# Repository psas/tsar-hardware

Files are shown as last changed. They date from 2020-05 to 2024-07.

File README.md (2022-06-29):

# Tsar Hardware
Hardware for the Test Stand Automation and Regulation project that runs [PSAS' Liquid Fuel Engine Test Stand](https://github.com/psas/liquid-engine-test-stand)

The TSAR system controls the test stand at a safe distance with several safety features in place. The system monitors the pressure, temperature, and valve states of the system. For automation software and controls see the [tsar software repo](https://github.com/psas/tsar-software). 

The OSGC Final UTEAP Report contains more detailed information and can be found [here](https://docs.google.com/document/d/1x4pjh9ZbApyyvRd1HysukK7K5CVWpYE1/edit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).

## Tsar Hardware System Architecture Block Diagrams

Below you can see the levels of block diagrams for the whole system,

### V -1

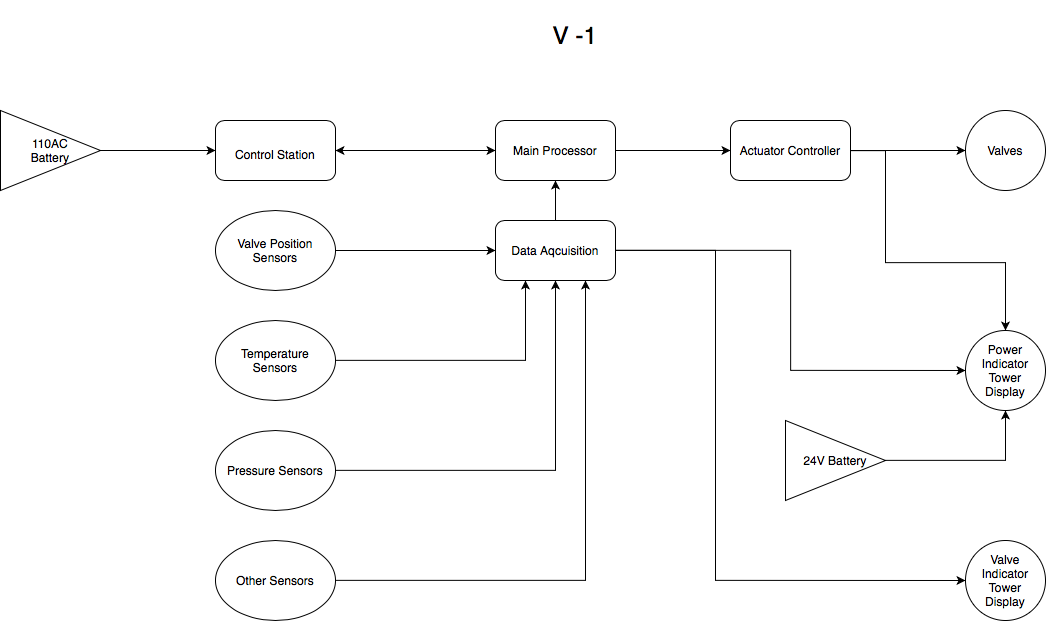
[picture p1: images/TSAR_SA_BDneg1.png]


### V 0

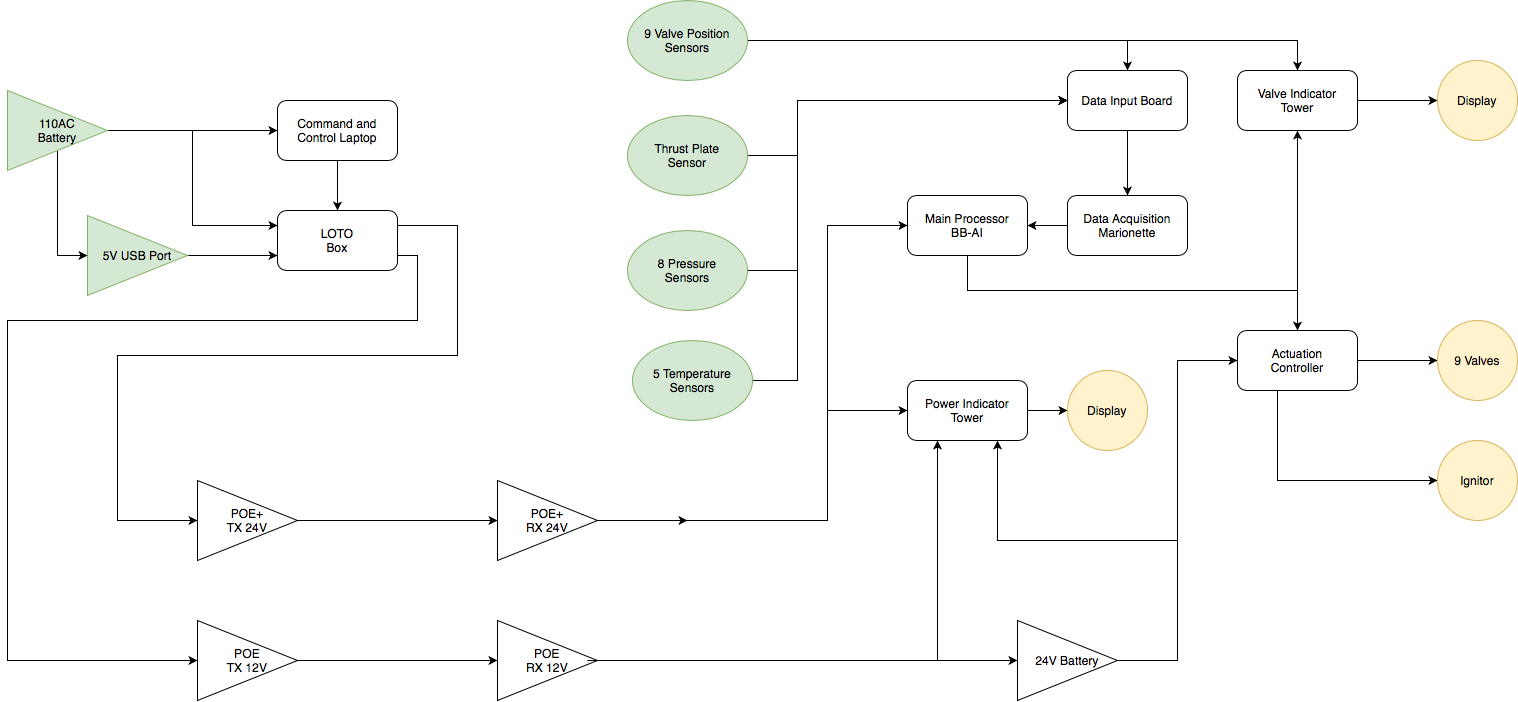
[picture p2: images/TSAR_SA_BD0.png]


### V 1

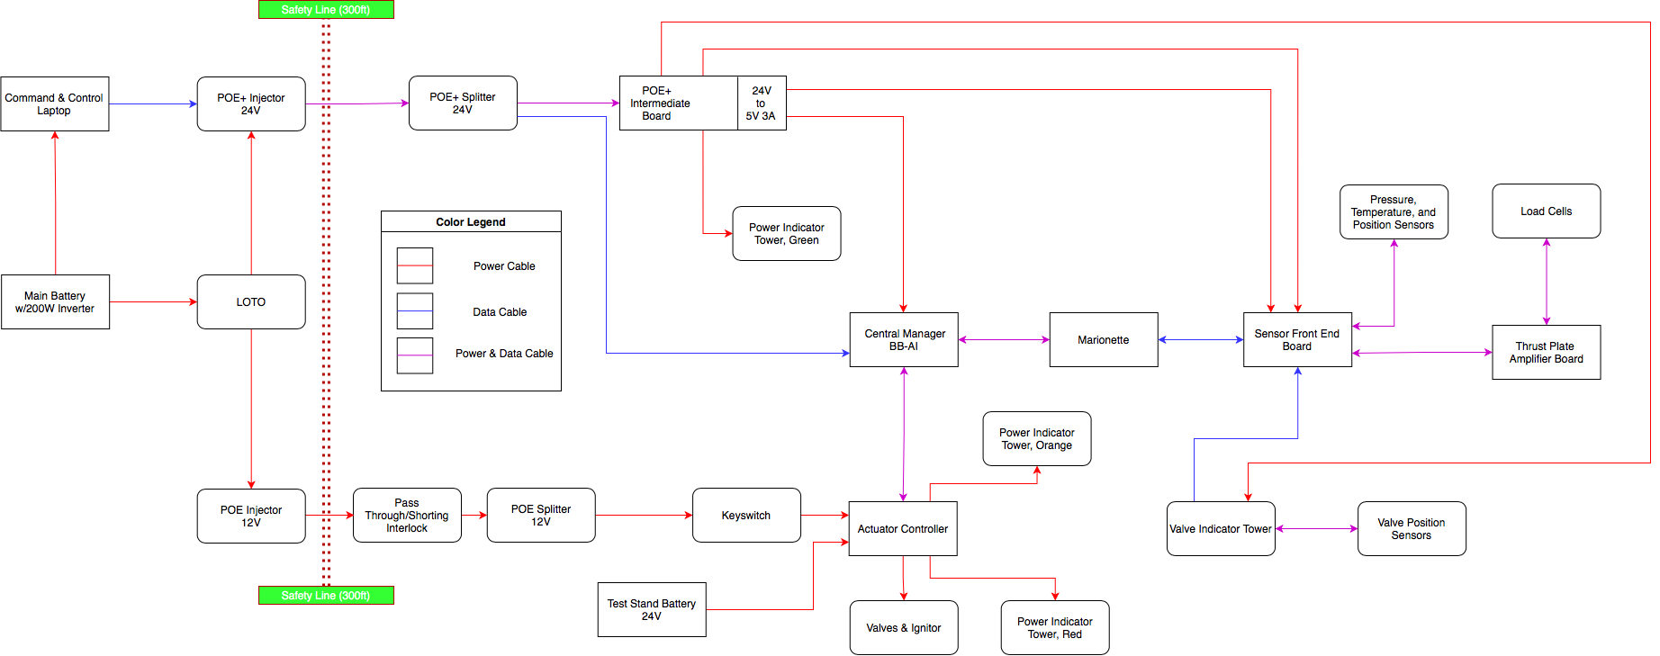
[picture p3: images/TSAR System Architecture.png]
sys_arch


## Systems Within the Repo

Within this repo there are several subsystems.

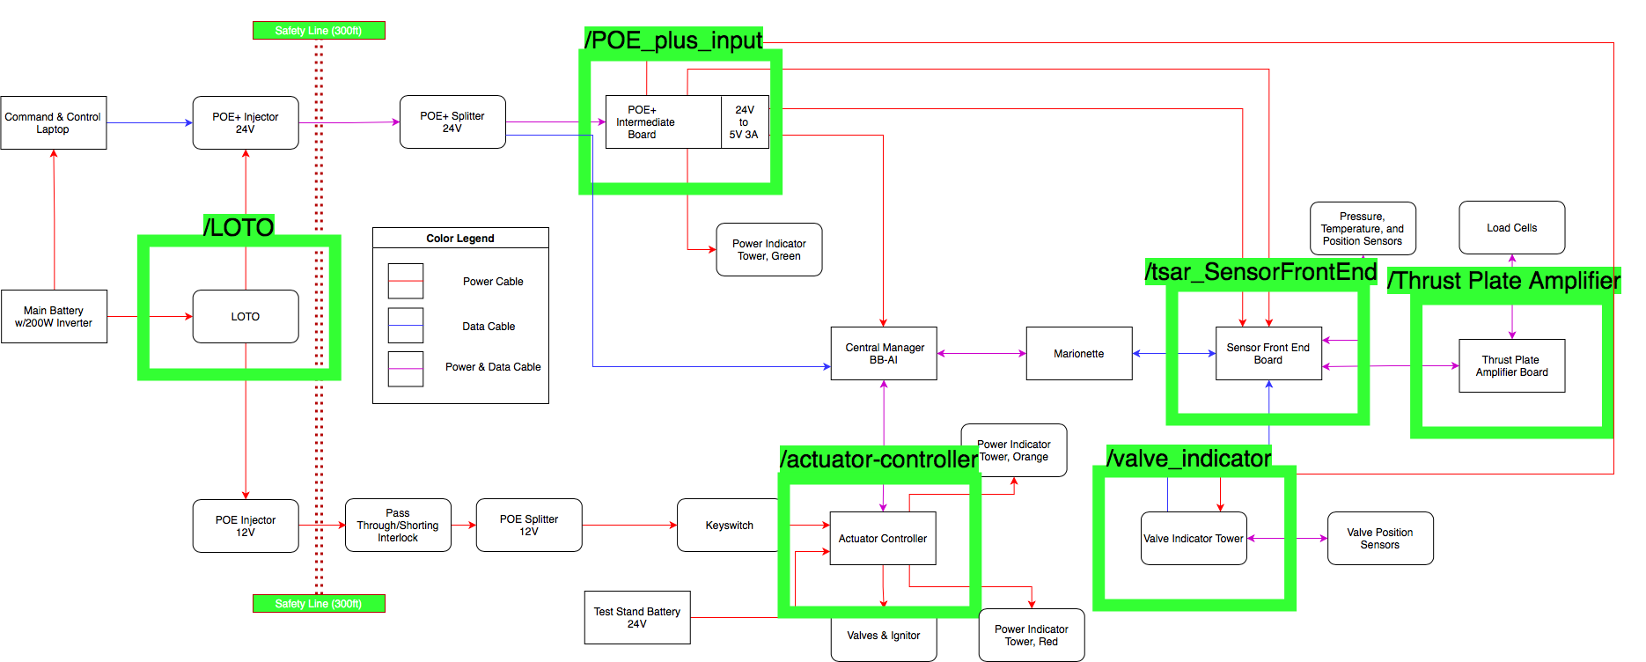
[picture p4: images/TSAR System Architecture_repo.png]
sys_arch


### [LOTO](https://github.com/psas/tsar-hardware/tree/master/LOTO)

The LOTO Repo is the Lock-Out Tag-Out subsystem.

This system prevents the test stand from being powered while key-holders are past the safety line. 

### [Thrust Plate Amplifier](https://github.com/psas/tsar-hardware/tree/master/Thrust%20Plate%20Amplifier)

The Thrust Plate Amplifier amplifies the thrust plate signal.

### [Actuator Controller](https://github.com/psas/tsar-hardware/tree/master/actuator-controller)

This board communicates with the BB-AI over UART and controls the valves. The processor is a STM32F0 using a Nucleo-board. 

For more information on the software for this board please see [Actuator Controller Code, Firmware](https://github.com/psas/tsar-software/tree/master/Actuator%20Controller%20Firmware) and [Actuator Controller Code, Test](https://github.com/psas/tsar-software/tree/master/Actuator%20Controller%20Test)

### [Tsar Sensor Front End](https://github.com/psas/tsar-hardware/tree/master/tsar_SensorFrontEnd)

This board collects the data from all of the sensors (temperature, pressure, thrust plate) and conditions the signals to send to the Marionette. 

### [Valve Indicator](https://github.com/psas/tsar-hardware/tree/master/valve_indicator)

This board collects the valve position data and compares it to the expected valve state. If there is an error it will display a code over LEDs to indicate which valve is misbehaving. 

For more information on the software for this board please see [Valve Indicator Code](https://github.com/psas/tsar-software/tree/master/valve_indicator)

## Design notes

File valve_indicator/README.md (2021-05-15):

# Eagle Schematics & Boards

## Valve Indicator

Purpose:
This board will collect valve position data using hall effect sensors mounted on nine solenoid valves and will report the current commanded state of the valves. 
The processor will compare the expected valve states with the correct reported valve states, 
if the states do not match the processor will output an indication over the LED arrays.
The LED arrays will display specific binary codes to indicate which valve does not match. 
If multiple valves do not match then the LED arrays will display all binary codes one after another based upon priority information.

Inputs:
- POE+ 24V Power
- UART Data
- Nine Hall Effect Sensors
- ST-Link V2 Emulator

Processor:
- STM32F042K

Outputs:
- Three LED Arrays
- One Buzzer
- SD Card Data Backup

### Libraries In Use

- Power Regulators: Diodes Inc. - AZ34063UMTR-G1.lbr
- Test Points: oresat-misc.lbr
- Processor: U-ST-STM32F042K-uC.lbr
- JTAG Emulator Connector: J-Samtec-FTSH-105-XXX-DV-K-ARM-SWD.lbr
- Diode: On Semiconductor - 1N5819G.lbr

### Design Rules

We are using the OshPark design rules for a 2-layer board.

### Safety Bar Level 0 Block Diagram:
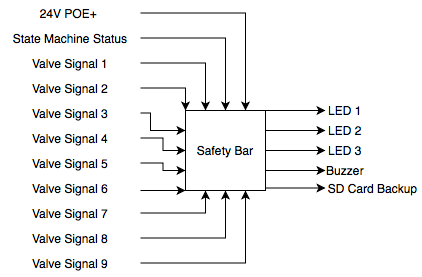
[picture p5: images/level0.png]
Level 0 Block Diagram


### Safety Bar Level 1 Block Diagram:
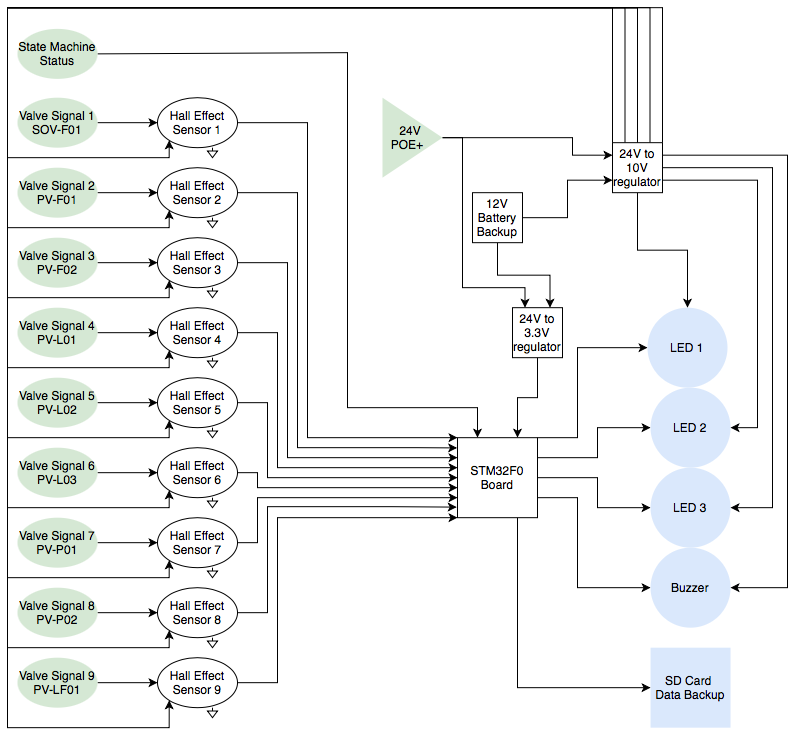
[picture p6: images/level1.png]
Level 2 Block Diagram


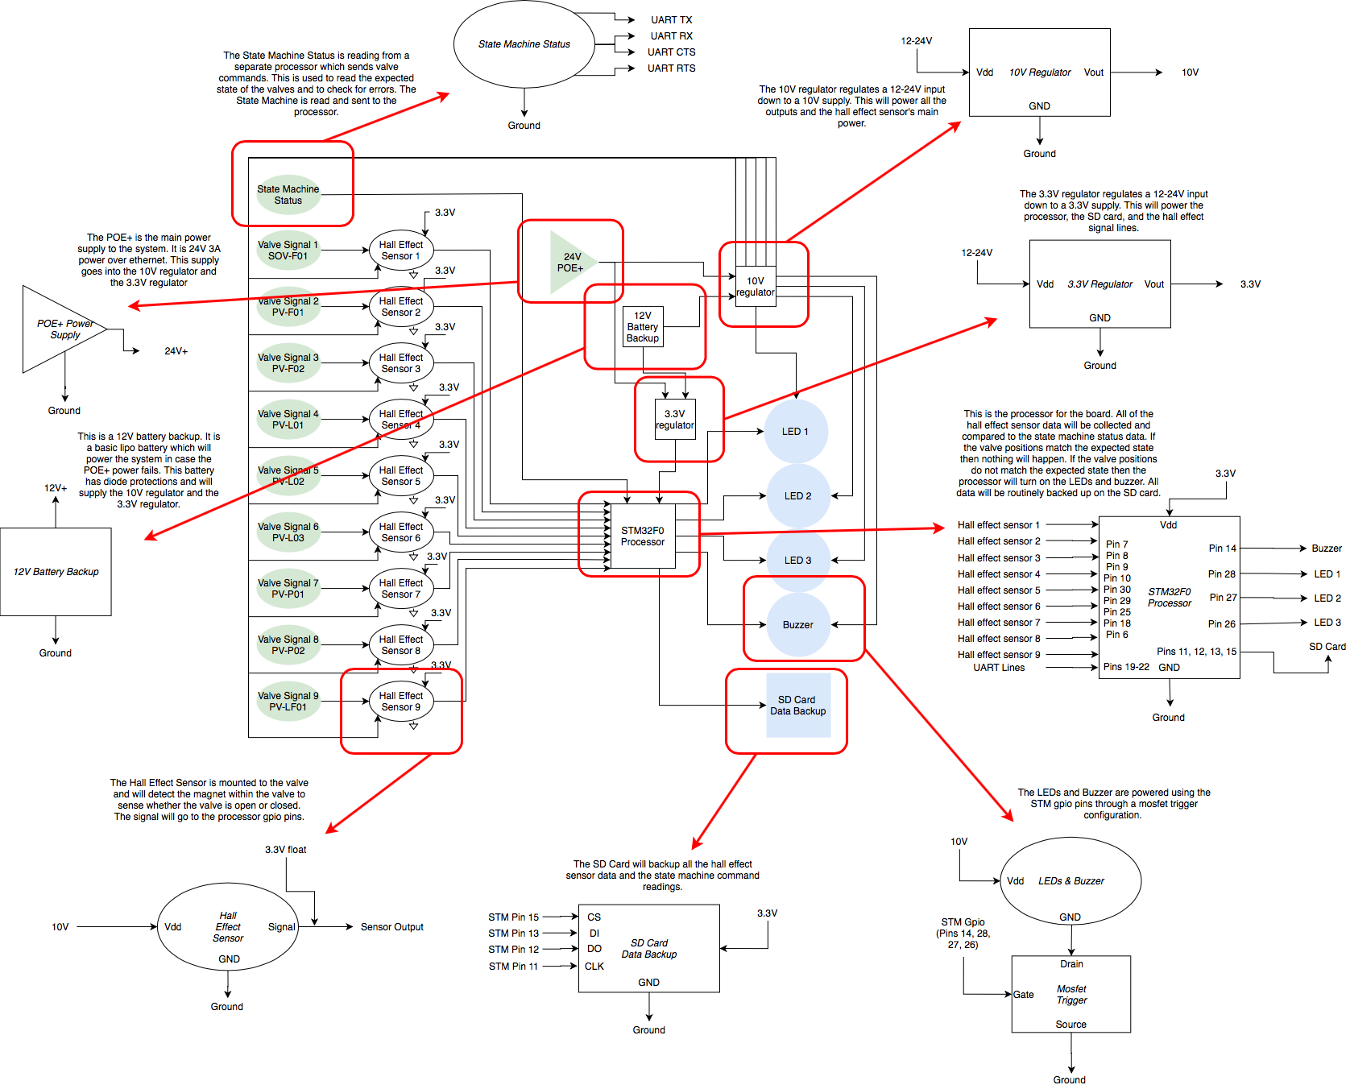
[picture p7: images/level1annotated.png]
Level 2 Block Diagram


### Extra Pinout
This board is equipped with a 32 pin header to access all unused STM32 pins.

1. PB2
2. +10V
3. PB10
4. PC9
5. PB11
6. PC8
7. PB12
8. PC1
9. PB13
10. PC10
11. PB14
12. PC4
13. PB15
14. PC5
15. PC11
16. PC6
17. GND
18. PC7
19. GND
20. PC12
21. PD2
22. PC3
23. PC14-OSC32_IN
24. BOOT0
25. PC13
26. PB9
27. +3V3
28. PC0
29. PC15_OSC32_OUT
30. PC2
31. GND
32. GND

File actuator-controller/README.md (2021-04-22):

# Actuator Controller

All valve and ignitor control is done via the Actuator Controller, which is currently implemented using a Nucleo mounted on a PCB. 

This board reads commands and data from the BeagleBone-AI over USB cable which it uses to switch test stand states and perform an Automatic Shutdown in the event of a system failure. Failure is defined as non-nominal sensor conditions; meaning that if pressure and/or temperature readings are outside of nominal ranges or if the physical state of the valves do not match the expected state of the valves (i.e. a valve is potentially stuck or frozen) then the system will go into an automatic shutdown state. The automatic shutdown state purges all propellants from the lines, depressurizes the system, and returns all valves to the Safety State (unpowered). This Automatic Shutdown can be triggered by the Actuator Controller automatically and it can be commanded by the user. 

The Actuator Controller requires a consistent heartbeat and emergency response code. If for some reason this heartbeat stops, or any other emergency indicator is tripped, the Actuator Controller will execute the emergency shutdown routine in accordance with the emergency response code most recently sent.

The Actuator Controller is also connected via UART to the Valve Indicator board. This connection is solely for sending the current state updates to the Valve Indicator board for other purposes. There is no data coming to the Actuator Controller from the Valve Indicator. 

The Nucleo board is powered by the USB cable from the BeagleBone-AI. The valves and ignitor are powered by a 24V power input coming from the Test Stand Battery. There is one 24V to 12V regulator on this board, it is used for an valve which runs at 12V; all other valves run at 24V. The 24V battery power is isolated from the Nucleo by the Mosfet circuits on sheet 2; the GPIO pins from the Nucleo trigger the Mosfets and allow the 24V power to switch on or restrict off the valves.

## Actuator Controller Block Diagram

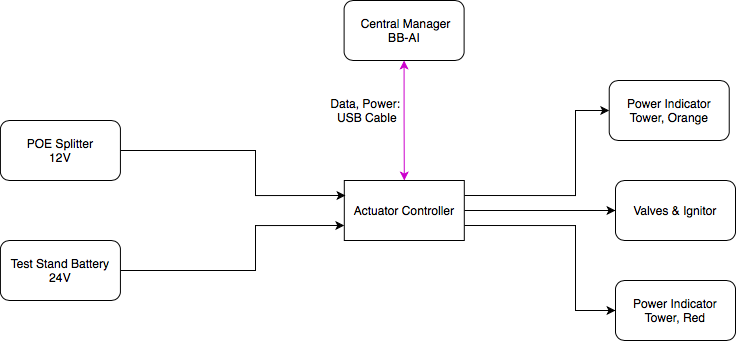
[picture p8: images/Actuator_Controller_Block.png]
ac_block


## Actuator Controller Software

All actuator control software and documentation can be found [here](https://github.com/psas/tsar-software). Specifically, [the testing software](https://github.com/psas/tsar-software/tree/master/Actuator%20Controller%20Test), [the firmware](https://github.com/psas/tsar-software/tree/master/Actuator%20Controller%20Firmware), and [the state machine](https://github.com/psas/tsar-software/tree/master/state-machine)

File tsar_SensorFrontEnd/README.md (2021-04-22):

The Sensor Front End board is an intermediate board which connects various test stand sensors to the data acquisition system. This board is intended to interface sensors with the Marionette DAQ Rev2.2. The Marionette documentation and board files can be found at https://marionette-daq.github.io/ 

The board allows connections for 44 analog sensors. These are broken into 14 channels which go through this board and to the Marionette board and 30 on this board, which connect to the Marionette via SPI.  Signals sent to the Marionette should be limited to the  0-3V range.

Currently (4/16/21), the 14 channels which go through this board and to the Marionette's ADC are  on sheet 2: Analog and consist of the 4 load cell sensors for thrust detection and 10 4-20mA pressure sensors which are labeled for either 1k PSI or 3k PSI. The signals go through TVS circuit protection before they are sent to the Marionette. The load cells are speced to TE Connectivity MPN: FC2311-0000-1000-L while the pressure sensors are speced to TE Connectivity 1k Sensors: 824-M305100000501KPG and 3k Sensors: M3051-000005-05KPG.

Currently (4/16/21), the 30 channels which are on this board go through TVS circuit protection, to an ADC chip (ADS7953QDBTRQ1), and then sent over SPI to the Marionette; these sensors can be found on sheet 3: Digital and sheet 4: Extra Sensors. These 30 channels consist of 7 thermocouples for temperature sensing, 9 hall effect sensors for valve position sensing, and 14 extra sensor lines which are unallocated. Note: The hall effect sensor lines come from the Valve Indicator board rather than directly from the sensors. 

The ADC channels on the Marionette sample 12-bits at up to 1Msps. The Front End board ADC channels sample 16-bits at 100ksps, which is sent to the Marionette over SPI.

There are 2 power regulators and two power inputs on this board. This board receives 24V from the POE Input Board and 5V from the POE Input Board. The two regulators take the 24V power and step it down to both 12V and 3V3. The 24V input serves as the main power source. The 12V power is used for the Pressure Sensors and is sent off board to the Thrust Plate Amplifier Board. The 5V power is used for the thermocouple amplifier circuits and the ADC reference voltage signal. The 3V3 line is used for the ADC chips. 

## Sensor Front End Block Diagram

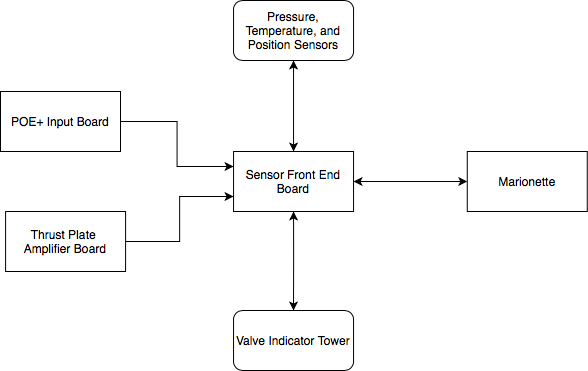
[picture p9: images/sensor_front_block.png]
Level 1 Block Diagram


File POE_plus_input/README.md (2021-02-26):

# POE Plus Input Board

This board takes the main low risk POE+ 24V input and splits it off to provide 24V power to the Valve Indicator Board and the Sensor Front End board. It has a 24V to 5V regulator which provides power to the Central Manager (BB-AI) and the Sensor Front End board. 

## POE+ Block Diagram

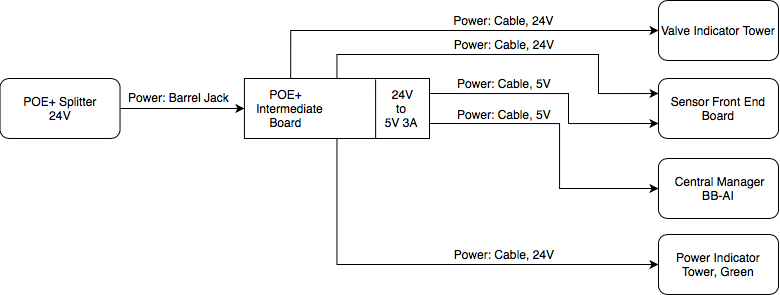
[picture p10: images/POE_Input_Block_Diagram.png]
Level 1 Block Diagram


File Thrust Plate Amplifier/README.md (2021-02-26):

# Thrust Plate Amplifier

This board amplifies the signals of the four load cells present on the thrust plate. The thrust plate measures the thrust of the liquid fuel engine. The load cells are compression only using part number FC2311-0000-1000-L. The signals from the amplifier are sent to the Sensor Front End board. This amplifier board must be as close as possible to the load cells on the thrust plate; otherwise the signals will be degraded and invalid. 

The thrust plate amplifier is powered by the Sensor Front End board's 12V rail.

## POE+ Block Diagram

Level 1 Block Diagram

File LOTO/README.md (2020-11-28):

# LOTO Key Indicator

There are nine of these boards mounted in the LOTO box. Each board indicates the safety keys status and powers the system if all safety keys are in place. There are LED indication lights, green indicates that the key is in place, red indicates that the key is not in place. 

## Level 0 Block Diagram

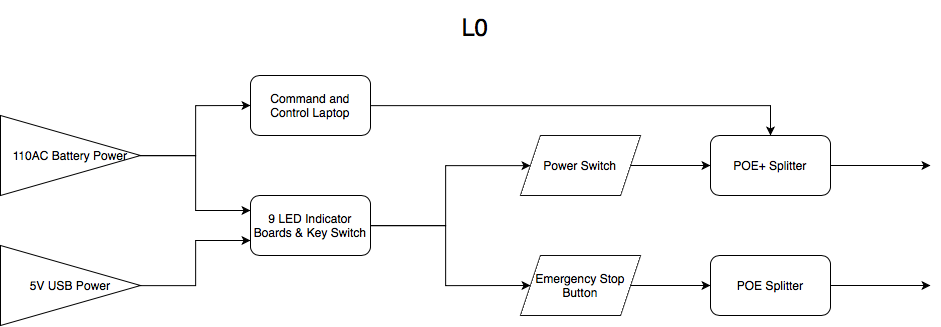
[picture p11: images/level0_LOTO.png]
l0loto


## Level 1 Block Diagram

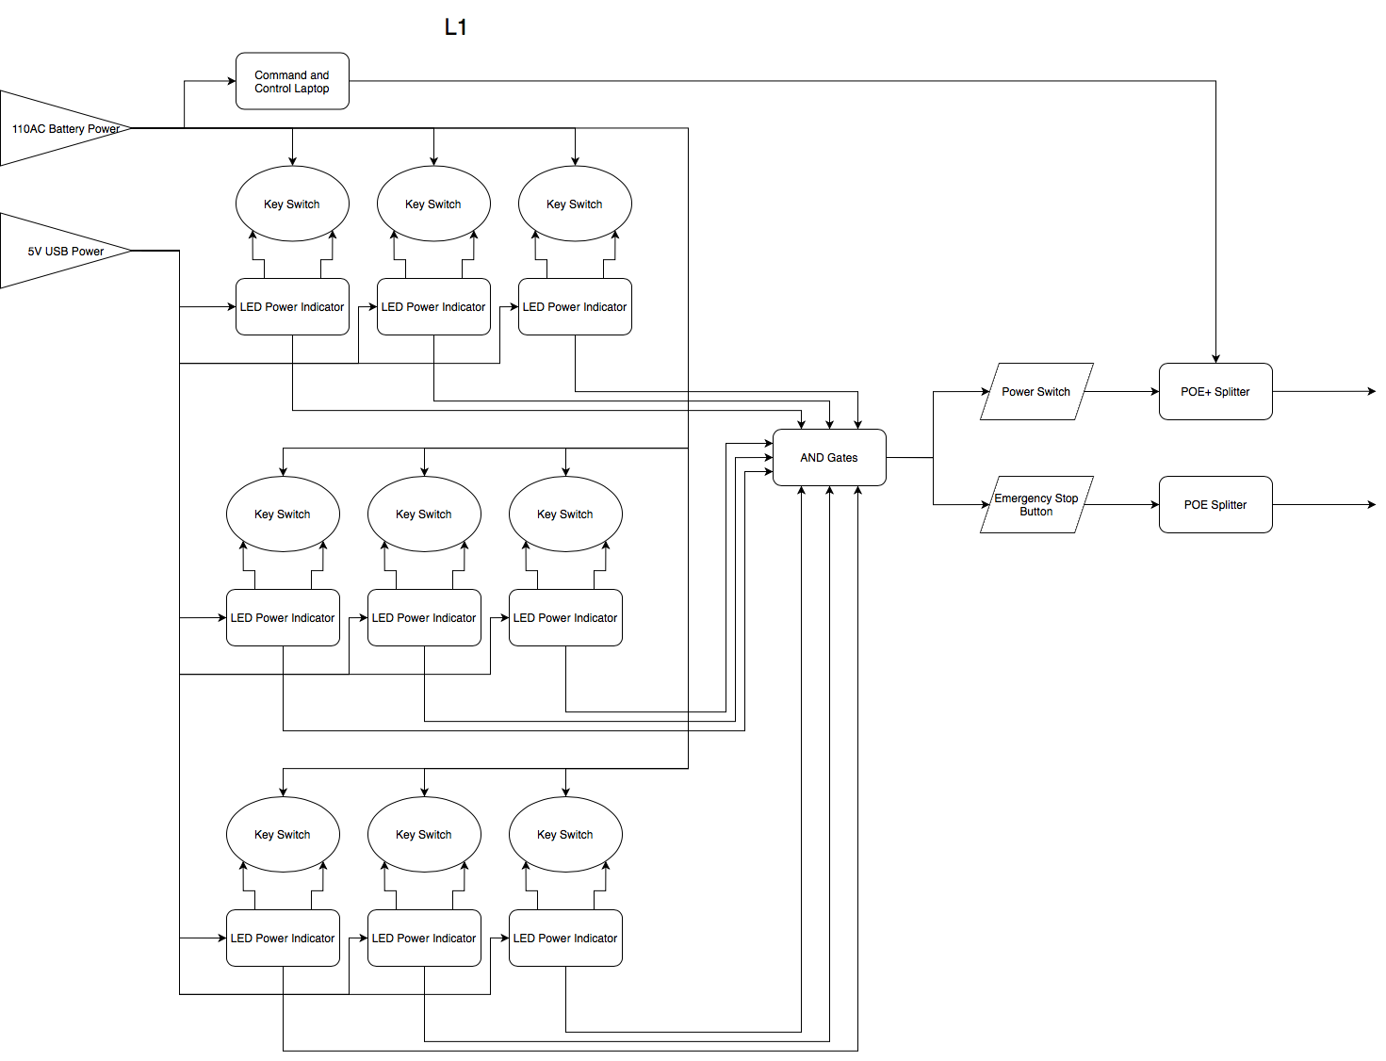
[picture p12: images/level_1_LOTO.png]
l1loto


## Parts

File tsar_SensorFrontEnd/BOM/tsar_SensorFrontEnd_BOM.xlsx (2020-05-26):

Status | Qty | Reference Designator | Description | Value | Manufacturer Part Number | Price (Individual) | Price X Quantity | Manufacturer | Product Link | Package
 | 26 | C1-C10, C16-C18, C20, C21, C28-C30, C35-C42 |  | 120 pF | C0805C121KDRACTU | $0.54 | $14.04 | Würth Elektronik | https://www.digikey.com/product-detail/en/kemet/C0805C121KDRACTU/399-7139-1-ND/3439332 | C0805
 | 6 | C12, C15, C23, C24, C27, C31 | 0.1uF Cap for 3V3/5V PSU | 0.1uF | GCM21BR72A104KA37L | $0.22 | $1.31 | Murata Electronics | DigiKey (https://www.digikey.com/product-detail/en/murata-electronics/GCM21BR72A104KA37L/490-4789-1-ND/1641708) | C0805
 | 6 | C11, C13, C14, C32-C34 |  | 1 uF | CL21A105KACLNNC | $0.15 | $0.90 | Samsung Electro-Mechanics | https://www.digikey.com/product-detail/en/samsung-electro-mechanics/CL21A105KACLNNC/1276-2395-1-ND/3890481 | C0805
 | 2 | C19, C25 | 10uF Cap for 3V3/5V PSU | 10uF | C0805C106K8PACTU | $0.12 | $0.23 | Murata Electronics | https://www.digikey.com/product-detail/en/murata-electronics/GRM21BR61E106KA73L/490-5523-1-ND/2334919 | C0805
 | 2 | C22, C26 |  | 4.7 uF | CL21A475KAQNNNE | $0.15 | $0.30 | Samsung Electro-Mechanics | https://www.digikey.com/product-detail/en/samsung-electro-mechanics/CL21A475KAQNNNE/1276-1244-1-ND/3889330 | C0805
 | 1 | POE_BYPASS | Bypass Cap from +12V POE | 100uF | ECA-1HM101 | $0.31 | $0.31 | Panasonic | https://www.digikey.com/product-detail/en/panasonic-electronic-components/ECA-1HM101/P5182-ND/245041 | Radial, Can
 | 26 | D1 - D26 | 5V TVS Diode | 5V TVS | D5V0H1U2LP1610-7 | $0.38 | $9.88 | Diodes Incorporated | https://www.digikey.com/product-detail/en/diodes-incorporated/D5V0H1U2LP1610-7/D5V0H1U2LP1610-7DICT-ND/8125969 | D0603
 | 2 | D27, D28 | Diode for Voltage Regulators | DFLS160 | DFLS160 | $0.44 | $0.88 | Diodes Incorporated | https://www.digikey.com/product-detail/en/diodes-incorporated/DFLS160-7/DFLS160DICT-ND/765636 | DO214AA
 | 27 | JP1 - JP27 | 1x 03 headers for unpopulated sensor channels |  |  |  |  |  |  | 3X 1 pin
 | 26 | R11-R20, R27-R29, R31, R32, R39, R40, R41, R47, R49, R54, R56, R58, R60- R62 | TVS Resistors for output | 1 K | RC0805FR-071KL | $0.10 | $2.60 | Yageo | https://www.digikey.com/product-detail/en/yageo/RC0805FR-071KL/311-1-00KCRCT-ND/730391 | R0805
 | 12 | R3-R10, R21-R24 | Pressure sensor Resistors, Cryo SensorResistors | 150 | RNCP0805FTD150R | $0.10 | $1.20 | Stackpole Electronics Inc | https://www.digikey.com/product-detail/en/stackpole-electronics-inc/RNCP0805FTD150R/RNCP0805FTD150RCT-ND/2240550 | R0805
 | 1 | R25 |  | 22k | RC0805FR-0722KL | $0.10 | $0.10 | Yageo | https://www.digikey.com/product-detail/en/yageo/RC0805FR-0722KL/311-22-0KCRCT-ND/730683 | R0805
 | 1 | R26 | Output-setting resistor for switching power supply | 124k | RK73H2ATTD1243F | $0.10 | $0.10 | KOA Speer Electronics, Inc. | https://www.digikey.com/product-detail/en/koa-speer-electronics-inc/RK73H2ATTD1243F/2019-RK73H2ATTD1243FCT-ND/10234967 | R0805
 | 2 | R30, R36 |  | 23.7k | RK73H2ATTD2372F | $0.10 | $0.20 | KOA Speer Electronics, Inc. | https://www.digikey.com/product-detail/en/koa-speer-electronics-inc/RK73H2ATTD2372F/2019-RK73H2ATTD2372FCT-ND/10235460 | R0805
 | 2 | R33, R37 |  | 10k | RN73R2ATTD1002F25 | $0.39 | $0.78 | KOA Speer Electronics, Inc. | https://www.digikey.com/product-detail/en/koa-speer-electronics-inc/RN73R2ATTD1002F25/2019-RN73R2ATTD1002F25CT-ND/11476953 | R0805
 | 1 | R35 |  | 73.2k | CRCW080573K2FKEA | $0.10 | $0.10 | Vishay Dale | https://www.digikey.com/product-detail/en/vishay-dale/CRCW080573K2FKEA/541-73-2KCCT-ND/1180997 | R0805
 | 2 | ANALOG_TO_DAQ, SERIAL_TO_DAQ | 40 pin connectors |  | SBH11-PBPC-D20-ST-BK | $0.73 | $1.46 | Sullins Connector Solutions | https://www.digikey.com/product-detail/en/sullins-connector-solutions/SBH11-PBPC-D20-ST-BK/S9175-ND/1990068
 | 2 | D29, D30 | BST Diode for 3v3/5V PSU | 1N4148W-7-F | 1N4148W-7-F | $0.16 | $0.32 | Diodes Incorporated | DigiKey (https://www.digikey.com/product-detail/en/diodes-incorporated/1N4148W-7-F/1N4148W-FDICT-ND/815280) | SOD-123
 | 1 | THRUST | 5-pin Molex connector for thrust data in | 22232051 | 22232051 | $0.34 | $0.34 | Molex | https://www.digikey.com/product-detail/en/molex/0022232051/WM4203-ND/26673 | 1X05_LONGPADS
 | 28 | Cryo1-4, Open1-11, PIT2, PIT5, PIT6, POE, PT1-5, Thrustpower, Ambient, OPENHS1, OPENHS2 | 2-pin Molex connector for 12V in | 22232021 | 22232021 | $0.17 | $4.76 | Molex | https://www.digikey.com/product-detail/en/molex/0022232021/900-0022232021-ND/26667 | 1X02_LONGPADS
 | 2 | L1, L2 | Inductor for switching power supply | 10uH | CLF5030NIT-100M-D | $1.09 | $2.18 | TDK Corporation | https://www.digikey.com/product-detail/en/tdk-corporation/CLF5030NIT-100M-D/445-174699-1-ND/6236888 | 0.209LX0.197"W(5.30MMX5.00MM)"
 | 2 | U$3, U$8 | ADC Chips | ADS8344N/1K | ADS8344N/1K | $15.52 | $31.04 | Texas Instruments | https://www.digikey.com/product-detail/en/texas-instruments/ADS8344N-1K/296-41197-1-ND/5222652 | 20SSOP
 | 2 | U$1, U$4 | IC REG BUCK ADJ 500MA TSOT23-6 | MP2456GJ-P | MP2456GJ-P | $1.65 | $3.30 | Monolithic Power Systems Inc. | https://www.digikey.com/product-detail/en/monolithic-power-systems-inc/MP2456GJ-P/1589-1120-1-ND/5298207 | TSOT-23-6
 |  |  |  |  |  |  | 76.338

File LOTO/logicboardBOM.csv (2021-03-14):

Qty | Parts | DIS | DPN | MFR | MPN
1 | JP1 | Digi-Key | A19439-ND | TE Connectivity AMP Connectors | 1-640454-2
2 | E_STOP, POE+_PS | Digi-Key | ED10561-ND | On Shore Technology Inc. | OSTVN02A150
2 | POE+_INJ, POE_INJ | Digi-Key | 900-0022232021-ND | Molex | 22232021
2 | R12, R16 | Digi-Key | 311-10.0KCRCT-ND | Yageo | RC0805FR-0710KL
9 | R_S1, R_S2, R_S3, R_S4, R_S5, R_S6, R_S7, R_S8, R_S9 | Digi-Key | P1.0KBYCT-ND | Panasonic Electronic Components | ERJ-PA3F1001V
2 | Q1, Q4 | Digi-Key | 1727-1142-1-ND | Nexperia USA Inc. | BSS138P,215
2 | R13, R21 | Digi-Key | RMCF0805FT28K0CT-ND | Stackpole Electronics Inc | RMCF0805FT28K0
2 | R1, R3 | Digi-Key | 311-4.70KCRCT-ND | Yageo | RC0805FR-074K7L
2 | U1, U2 | Digi-Key | 296-31524-1-ND | Texas Instruments | CD4082BNSR
2 | D1, D2 | Digi-Key | 1514-CMHSH5-4TRPBFREECT-ND | Central Semiconductor Corp | CMHSH5-4 TR PBFREE
2 | Q2, Q3 | Digi-Key | IRF9530NPBF-ND | Infineon Technologies | IRF9530NPBF
4 | H1, H2, H3, H4

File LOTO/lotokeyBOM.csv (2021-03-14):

Qty | Parts | DIS | DPN | MFR | MPN
1 | JP11 | Digi-Key | A19439-ND | TE Connectivity AMP Connectors | 1-640454-2
10 | JP1, JP2, JP3, JP4, JP5, JP6, JP7, JP8, JP9, JP10 | Digi-Key | ED10561-ND | On Shore Technology Inc. | OSTVN02A150
9 | R2, R5, R8, R11, R14, R17, R20, R23, R26 | Digi-Key | 749-2062-1-ND | Vishay Beyschlag/Draloric/BC Components | CCF5510K0FKE36
9 | C3, C6, C9, C12, C15, C18, C21, C24, C27 | Digi-Key | 445-181284-1-ND | TDK Corporation | FG28X5R1E106MRT06
18 | R1, R3, R4, R6, R7, R9, R10, R12, R13, R15, R16, R18, R19, R21, R22, R24, R25, R27 | Digi-Key | 749-2068-1-ND | Vishay Beyschlag/Draloric/BC Components | CCF551K00FKE36
18 | C1, C2, C4, C5, C7, C8, C10, C11, C13, C14, C16, C17, C19, C20, C22, C23, C25, C26 | Digi-Key | 445-173577-1-ND | TDK Corporation | FG28X5R1E475KRT06
9 | L1, L2, L3, L4, L5, L6, L7, L8, L9 | Digi-Key | 495-5572-1-ND | EPCOS - TDK Electronics | B78108S1682K000
9 | PMOS, PMOS1, PMOS2, PMOS3, PMOS4, PMOS5, PMOS6, PMOS7, PMOS8 | Digi-Key | TP2104N3-G-ND | Microchip Technology | TP2104N3-G
9 | NMOS, NMOS1, NMOS2, NMOS3, NMOS4, NMOS5, NMOS6, NMOS7, NMOS8 | Digi-Key | 2N7000-G-ND | Microchip Technology | 2N7000-G
9 | PS1, PS2, PS3, PS4, PS5, PS6, PS7, PS8, PS9 | Digi-Key | 102-6291-ND | CUI Inc. | PDSE1-S5-S5-S
9 | RED, RED1, RED2, RED3, RED4, RED5, RED6, RED7, RED8 | Digi-Key | TLUR6400-ND | Vishay Semiconductor Opto Division | TLUR6400
9 | GREEN, GREEN1, GREEN2, GREEN3, GREEN4, GREEN5, GREEN6, GREEN7, GREEN8 | Digi-Key | TLHG5200-ND | Vishay Semiconductor Opto Division | TLHG5200

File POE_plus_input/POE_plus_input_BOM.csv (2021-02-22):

Qty | Parts | DIS | DPN | MFR | MPN
5 | BBAI_5V, PIT_GREEN, SFE_5V, SFE_24V, VI_24V | Digi-Key | WM10560CT-ND | Molex | 1718573002
8 | H1, H2, H3, H4, H5, H6, H7, H8
1 | BOOST_CAP | Digi-Key | 478-5007-1-ND | AVX Corporation | 06035C103JAT2A
1 | C_IN3 | Digi-Key | 587-3171-1-ND | Taiyo Yuden | UMK107ABJ474KA-T
1 | C_OUT1 | Digi-Key | 587-5426-1-ND | Taiyo Yuden | EMK325ABJ107MM-P
1 | C_IN2 | Digi-Key | 565-3335-1-ND | United Chemi-Con | KTS500B156M55N0T00
1 | C_IN1 | Digi-Key | 565-3335-1-ND | United Chemi-Con | KTS500B156M55N0T00
1 | SOFTSTART | Digi-Key | 1276-1091-1-ND | Samsung Electro-Mechanics | CL10C102JB8NNNC
1 | POE_IN | Digi-Key | 2092-KLDX-SMT2-0202-ACT-ND | Kycon, Inc. | KLDX-SMT2-0202-ATR
1 | C_OUT2 | Digi-Key | 445-6002-1-ND | TDK Corporation | C3216X5R1C336M160AB
1 | L1 | Digi-Key | 553-1406-ND | Pulse Electronics Power | PE-53823SNL
1 | C_OUT | Digi-Key | 490-16309-1-ND | Murata Electronics | GRM32EC81C476KE15K
1 | I_LIM_ADJ | Digi-Key | 311-8.20KFRCT-ND | Yageo | RC1206FR-078K2L
1 | U1 | Digi-Key | LM2673SX-5.0/NOPBCT-ND | Texas Instruments | LM2673SX-5.0/NOPB
1 | D1 | Digi-Key | SR305-TPMSCT-ND | Micro Commercial Co | SR305-TP

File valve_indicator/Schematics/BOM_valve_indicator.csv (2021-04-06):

Qty | Parts | DIS | DPN | MFR | MPN
1 | IC1 | Digi-Key | 296-9214-5-ND | Texas Instruments | CD74HC4050M
1 | SD | Digi-Key | 350-2035-1-ND | Dialight | 5988070107F
1 | X2 | Digi-Key | 2073-MEM2061-01-188-00-ACT-ND | GCT | MEM2061-01-188-00-A
1 | JP3 | Digi-Key | WM10196-ND | Molex | 1718570012
1 | JP2 | Digi-Key | S2011EC-16-ND | Sullins Connector Solutions | PRPC016DAAN-RC
1 | JP1 | Digi-Key | AE11083-ND | Molex | AWHW 10A-0202-T
2 | RS_H, RS_L | Digi-Key | P.33AJCT-ND | Panasonic Electronic Components | ERJ-3RQFR33V
1 | R19 | Digi-Key | P100KADCT-ND | Panasonic Electronic Components | ERJ-P06J104V
6 | C10, C11, C12, C53, C54, C55 | Digi-Key | 1276-1006-1-ND | Samsung Electro-Mechanics | CL10B104KA8NNNC
1 | R2_H | Digi-Key | P105KAACT-ND | Panasonic Electronic Components | ERJ-14NF1053U
15 | R1, R2, R3, R4, R5, R6, R7, R8, R9, R14, R15, R16, R17, R18, R20 | Digi-Key | RMCF0603FT10K0CT-ND | Stackpole Electronics Inc | RMCF0603FT10K0
10 | C34, C35, C36, C37, C38, C39, C40, C41, C42, C43 | Digi-Key | 490-18664-1-ND | Murata Electronics | GRM21BR61H106ME43L
1 | C58 | Digi-Key | 1276-6456-1-ND | Samsung Electro-Mechanics | CL21A106KPFNNNG
10 | C13, C14, C15, C16, C17, C18, C19, C20, C21, C22 | Digi-Key | 1276-2876-1-ND | Samsung Electro-Mechanics | CL31A106KBHNNNE
2 | R1_H, R1_L | Digi-Key | 541-15.0KTCT-ND | Vishay Dale | CRCW080515K0FKEAHP
2 | D1, D2 | Digi-Key | 1N5819HW-FDICT-ND | Diodes Incorporated | 1N5819HW-7-F
4 | R23, R24, R26, R27 | Digi-Key | 511-1732-1-ND | Rohm Semiconductor | SDR03EZPJ102
4 | R10, R11, R12, R13 | Digi-Key | RMCF0603JJ1K00CT-ND | Stackpole Electronics Inc | RMCF0603JJ1K00
1 | R21 | Digi-Key | RMCF0603JJ1K00CT-ND | Stackpole Electronics Inc | RMCF0603JJ1K00
1 | R25 | Digi-Key | RHM20KDCT-ND | Rohm Semiconductor | ESR03EZPJ203
2 | C56, C57 | Digi-Key | 399-8786-1-ND | KEMET | CBR04C200F5GAC
2 | L1, L2 | Digi-Key | 811-2101-ND | Murata Power Solutions Inc. | 12RS224C
1 | R2_L | Digi-Key | 541-24.9KTCT-ND | Vishay Dale | CRCW080524K9FKEAHP
1 | POE_IN | Digi-Key | 2092-KLDX-SMT2-0202-ACT-ND | Kycon, Inc. | KLDX-SMT2-0202-ATR
1 | C1 | Digi-Key | 445-7400-1-ND | TDK Corporation | C1608C0G1H472J080AA
8 | C2, C3, C4, C5, C6, C7, C8, C9 | Digi-Key | 445-7400-1-ND | TDK Corporation | C1608C0G1H472J080AA
2 | C2_H, C2_L | Digi-Key | 1292-1438-1-ND | Walsin Technology Corporation | 0603B471K500CT
10 | C24, C25, C26, C27, C28, C29, C30, C31, C32, C33 | Digi-Key | 445-8239-1-ND | TDK Corporation | C2012X5R1A476M125AC
10 | C23, C44, C45, C46, C47, C48, C49, C50, C51, C52 | Digi-Key | 445-8047-1-ND | TDK Corporation | C3216X5R1E476M160AC
2 | D5, D6 | Digi-Key | B240A-FDICT-ND | Diodes Incorporated | B240A-13-F
1 | X1 | Digi-Key | XC2181CT-ND | ECS Inc. | ECS-160-10-36Q-ES-TR
1 | CM1 | Digi-Key | SAM13160CT-ND | Samtec Inc. | FTSH-105-01-F-DV-K-TR
4 | 3V3., 10V., POE., VBATT. | Digi-Key | 350-2035-1-ND | Dialight | 5988070107F
1 | HES1 | Digi-Key | WM10158-ND | Molex | 1718570003
1 | HES2 | Digi-Key | WM10158-ND | Molex | 1718570003
1 | HES3 | Digi-Key | WM10158-ND | Molex | 1718570003
1 | HES4 | Digi-Key | WM10158-ND | Molex | 1718570003
1 | HES5 | Digi-Key | WM10158-ND | Molex | 1718570003
1 | HES6 | Digi-Key | WM10158-ND | Molex | 1718570003
1 | HES7 | Digi-Key | WM10158-ND | Molex | 1718570003
1 | HES8 | Digi-Key | WM10158-ND | Molex | 1718570003
1 | HES9 | Digi-Key | WM10158-ND | Molex | 1718570003
1 | Q5 | Digi-Key | FQP17P10-ND | ON Semiconductor | FQP17P10
1 | BATT | Digi-Key | 900-0022232021-ND | Molex | 22232021
2 | U1, U2 | Digi-Key | 296-17763-1-ND | Texas Instruments | MC33063ADR
5 | Q1, Q2, Q3, Q4, Q6 | Digi-Key | 1727-2307-1-ND | Nexperia USA Inc. | PMV45EN2R
1 | SM_STAT | Digi-Key | AE11083-ND | Molex | AWHW 10A-0202-T
1 | U4 | Digi-Key | 497-15877-ND | STMicroelectronics | STM32L476RGT6

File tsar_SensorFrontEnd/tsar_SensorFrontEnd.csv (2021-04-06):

Qty | Parts | DIS | DPN | MFR | MPN
1 | L1 | Digi-Key | 445-174699-1-ND | TDK Corporation | CLF5030NIT-100M-D
1 | TO_VI | Digi-Key | WM10196-ND | Molex | 1718570012
1 | POE_IN_5V | Digi-Key | 900-0022232021-ND | Molex | 22232021
1 | JP1 | Digi-Key | S2011EC-12-ND | Sullins Connector Solutions | PRPC012DAAN-RC
4 | R80, R81, R82, R83 | Digi-Key | 541-2779-1-ND | Vishay Dale | RCS06030000Z0EA
14 | C16, C17, C19, C21, C23, C28, C34, C44, C55, C56, C59, C60, C63, C64 | Digi-Key | 1276-1009-1-ND | Samsung Electro-Mechanics | CL10B103KB8NNNC
17 | C12, C18, C20, C22, C24, C27, C29, C31, C46, C48, C54, C57, C58, C61, C62, C65, C66 | Digi-Key | 1276-CL10B104KB8NNNLCT-ND | Samsung Electro-Mechanics | CL10B104KB8NNNL
7 | R21, R25, R29, R33, R39, R50, R55 | Digi-Key | 2019-SG73P1JTTD1000FCT-ND | KOA Speer Electronics, Inc. | SG73P1JTTD1000F
7 | R22, R26, R30, R34, R40, R51, R57 | Digi-Key | 2019-SG73P1JTTD1000FCT-ND | Stackpole Electronics Inc | SG73P1JTTD1000F
1 | C43 | Digi-Key | 1276-CL10B104KB8NNNLCT-ND | Samsung Electro-Mechanics | CL10B104KB8NNNL
1 | POE_BYPASS | Digi-Key | P5182-ND | Panasonic Electronic Components | ECA-1HM101
1 | R37 | Digi-Key | RHM10KADCT-ND | Rohm Semiconductor | ESR03EZPF1002
3 | C25, C52, C53 | Digi-Key | 1276-6736-1-ND | Samsung Electro-Mechanics | CL31A106MBHNNNE
1 | R69 | Digi-Key | 2019-RK73H2ATTD1133FCT-ND | KOA Speer Electronics, Inc. | RK73H2ATTD1133F
33 | C1, C2, C3, C4, C5, C6, C7, C8, C9, C10, C30, C35, C36, C37, C38, C39, C40, C41, C42, C70, C71, C73, C74, C75, C76, C77, C78, C79, C80, C83, C84, C85, C86 | Digi-Key | 1276-1160-1-ND | Samsung Electro-Mechanics | CL10C121JB8NNNC
10 | R1, R2, R3, R4, R5, R6, R7, R8, R9, R10 | Digi-Key | A110464CT-ND | TE Connectivity Passive Product | 4-2176091-1
7 | R24, R28, R32, R43, R48, R53, R63 | Digi-Key | 511-1732-1-ND | Stackpole Electronics Inc | SDR03EZPJ102
7 | R23, R27, R31, R42, R44, R52, R59 | Digi-Key | 118-CMP0603-FX-1004ELFCT-ND | Bourns Inc. | CMP0603-FX-1004ELF
1 | D30 | Digi-Key | 1N4148W-FDICT-ND | Diodes Incorporated | 1N4148W-7-F
35 | R11, R12, R13, R14, R15, R16, R17, R18, R19, R20, R41, R46, R47, R49, R54, R56, R58, R60, R61, R62, R65, R66, R68, R70, R71, R72, R73, R74, R78, R79, R84, R88, R89, R90, R91 | Digi-Key | P1.0KBYCT-ND | Panasonic Electronic Components | ERJ-PA3F1001V
1 | C67 | Digi-Key | 1276-1102-1-ND | Samsung Electro-Mechanics | CL10A105KA8NNNC
6 | C11, C13, C14, C15, C32, C33 | Digi-Key | 1276-1860-1-ND | Samsung Electro-Mechanics | CL10A105KB8NNNC
2 | C50, C51 | Digi-Key | 1276-1860-1-ND | Samsung Electro-Mechanics | CL10A105KB8NNNC
2 | R45, R85 | Digi-Key | P20KBZCT-ND | Panasonic Electronic Components | ERJ-PA3J203V
2 | POE, THRUSTPOWER | Digi-Key | 900-0022232021-ND | Molex | 22-23-2021
16 | PT-F02, PT-F03, PT-F04, PT-L01, PT-L02, PT-L03, PT-L04, PT-M01, PT-M02, TT-F01, TT-F02, TT-L01, TT-L02, TT-L03, TT-L04, TT-L05 | Digi-Key | 900-0022232021-ND | Molex | 22-23-2021
1 | PT-F01 | Digi-Key | 900-0022232021-ND | Molex | 22-23-2021
1 | TP | Digi-Key | WM4203-ND | Molex | 22-23-2051
1 | C68 | Digi-Key | 490-10468-1-ND | Murata Electronics | GRM188C60J226MEA0D
1 | R36 | Digi-Key | 2019-RK73H2ATTD2372FCT-ND | KOA Speer Electronics, Inc. | RK73H2ATTD2372F
1 | L3 | Digi-Key | 553-PM4340.333NLTCT-ND | Pulse Electronics Power | PM4340.333NLT
2 | C26, C45 | Digi-Key | 1276-1248-1-ND | Samsung Electro-Mechanics | CL21A475KBQNNNE
2 | C47, C49 | Digi-Key | 445-1277-1-ND | TDK Corporation | C1608C0G1H470J080AA
1 | R76 | Digi-Key | BC4966CT-ND | Vishay Dale | CRMA1206AF500KFKEF
1 | R35 | Digi-Key | 2019-RK73H2ATTD7322FCT-ND | KOA Speer Electronics, Inc. | RK73H2ATTD7322F
1 | R75 | Digi-Key | 2019-RK73H2ATTD8201FCT-ND | KOA Speer Electronics, Inc. | RK73H2ATTD8201F
7 | U1, U2, U5, U6, U7, U8, U9 | Digi-Key | AD8495ARMZ-ND | Analog Devices Inc. | AD8495ARMZ
2 | U3, U4 | Digi-Key | 296-50898-1-ND | Texas Instruments | ADS7953QDBTRQ1
33 | D1, D8, D9, D10, D11, D12, D13, D14, D15, D16, D17, D19, D20, D21, D22, D23, D24, D25, D26, D32, D33, D34, D35, D36, D37, D38, D39, D41, D42, D44, D45, D46, D47 | Digi-Key | D5V0H1U2LP1610-7DICT-ND | Diodes Incorporated | D5V0H1U2LP1610-7
2 | D27, D31 | Digi-Key | DFLS160DICT-ND | Diodes Incorporated | DFLS160-7
4 | 3V3., 5V., 12V., POE+. | Digi-Key | 350-2035-1-ND | Dialight | 5988070107F
2 | ANALOG_TO_DAQ, SERIAL_TO_DAQ | Digi-Key | S9175-ND | Sullins Connector Solutions | SBH11-PBPC-D20-ST-BK
2 | U$2, U$4 | Digi-Key | 1589-1120-1-ND | Monolithic Power Systems Inc. | MP2456GJ-P
1 | R77
1 | R38
1 | U10 | Digi-Key | 296-39165-1-ND | Texas Instruments | REF5025AIDR
7 | D2, D3, D4, D5, D6, D7, D28 | Digi-Key | 497-13181-1-ND | STMicroelectronics | TLVH431AIL3T

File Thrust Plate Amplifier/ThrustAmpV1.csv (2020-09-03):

Qty | Value | Parts | DIS | DPN | MFR | MPN
1 |  | J1 | Digi-Key | 900-0022232021-ND | Molex | 22232021
4 |  | J4, J5, J6, J7 | Digi-Key | WM4202-ND | Molex | 22232041
1 |  | J2 | Digi-Key | WM4203-ND | Molex | 22232051
1 |  | D9 | Digi-Key | D12V0H1U2LP1610-7DICT-ND | Diodes Incorporated | D12V0H1U2LP1610-7
14 |  | D2, D3, D4, D5, D6, D7, D8, D10, D11, D12, D13, D14, D15, D16 | Digi-Key | D5V0H1U2LP1610-7DICT-ND | Diodes Incorporated | D5V0H1U2LP1610-7
4 | #4-BARE_MOUNTING_HOLE/.300 | H5, H6, H7, H8
4 | 1 K | R13, R18, R19, R20 | Digi-Key | 311-1.00KCRCT-ND | Yageo | RC0805FR-071KL
2 | 1 uF | C5, C12 | Digi-Key | 1276-2395-1-ND | Samsung Electro-Mechanics | CL21A105KACLNNC
2 | 10 nF | C4, C11 | Digi-Key | 445-14445-1-ND | TDK Corporation | C2012X5R2E103K125AA
1 | 100 nF | C2 | Digi-Key | 478-12790-1-ND | AVX Corporation | 08055D104KAT2A
7 | 100 nF | C7, C8, C9, C10, C19, C20, C22 | Digi-Key | 478-12790-1-ND | AVX Corporation | 08055D104KAT2A
8 | 100 pF | C18, C23, C24, C25, C26, C27, C28, C29 | Digi-Key | 732-8046-1-ND | Würth Elektronik | 885012207054
1 | 10BQ060TR | D1 | Digi-Key | 1655-1342-1-ND | SMC Diode Solutions | 10BQ060TR
4 | 120 pF | C14, C15, C16, C17 | Digi-Key | 399-7139-1-ND | KEMET | C0805C121KDRACTU
1 | 124k | R16 | Digi-Key | 2019-RK73H2ATTD1243FCT-ND | KOA Speer Electronics, Inc. | RK73H2ATTD1243F
1 | 19.1 k | R14 | Digi-Key | RNCP0805FTD19K1CT-ND | Stackpole Electronics Inc | RNCP0805FTD19K1
1 | 1N4148W-7-F | CR1 | Digi-Key | 1N4148W-FDICT-ND | Diodes Incorporated | 1N4148W-7-F
2 | 2.2 uF | C6, C13 | Digi-Key | 1276-6458-1-ND | Samsung Electro-Mechanics | CL21A225KAFNNNG
1 | 22 uF | C3 | Digi-Key | 1276-6786-1-ND | Samsung Electro-Mechanics | CL21A226KPCLRNC
1 | 4.7 uF | C1 | Digi-Key | 1276-1244-1-ND | Samsung Electro-Mechanics | CL21A475KAQNNNE
1 | 499 k | R17 | Digi-Key | 2019-RK73H2ATTD4993FCT-ND | KOA Speer Electronics, Inc. | RK73H2ATTD4993F
1 | CLF5030NIT-100M-D | U$2 | Digi-Key | 445-174699-1-ND | TDK Corporation | CLF5030NIT-100M-D
4 | INA126PA | U1, U2, U3, U4 | Digi-Key | INA126PA-ND | Texas Instruments | INA126PA
1 | LP2985AIM5-3.3 | U5 | Digi-Key | LP2985AIM5-3.3/NOPBCT-ND | Texas Instruments | LP2985AIM5-3.3/NOPB
1 | LP2985AIM5-5.0/NOPB | U6 | Digi-Key | LP2985AIM5-5.0/NOPBCT-ND | Texas Instruments | LP2985AIM5-5.0/NOPB
1 | MP2456GJ-P | U$1 | Digi-Key | 1589-1120-1-ND | Monolithic Power Systems Inc. | MP2456GJ-P
8 | NP | R5, R6, R7, R8, R9, R10, R11, R12
1 | NP | R15
4 | TBD | R1, R2, R3, R4
4 | TEST-POINTTP_15TH_THRU | TP1, TP2, TP3, TP4

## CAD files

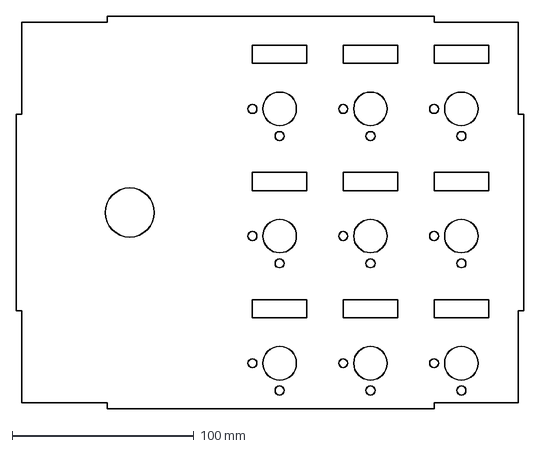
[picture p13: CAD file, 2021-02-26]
Board_Outlines/LOTO.dxf
279.4 x 215.9 mm

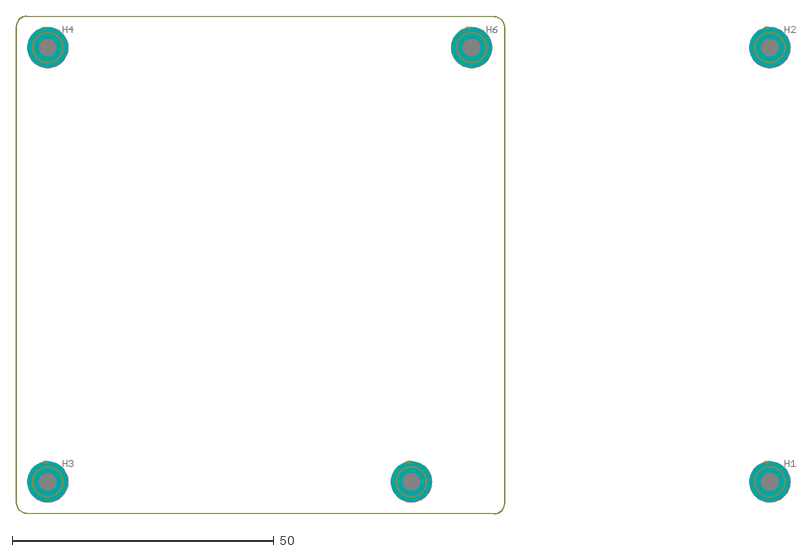
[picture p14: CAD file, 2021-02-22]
Board_Outlines/marionette_dxf_small.dxf
148.9 x 95.1

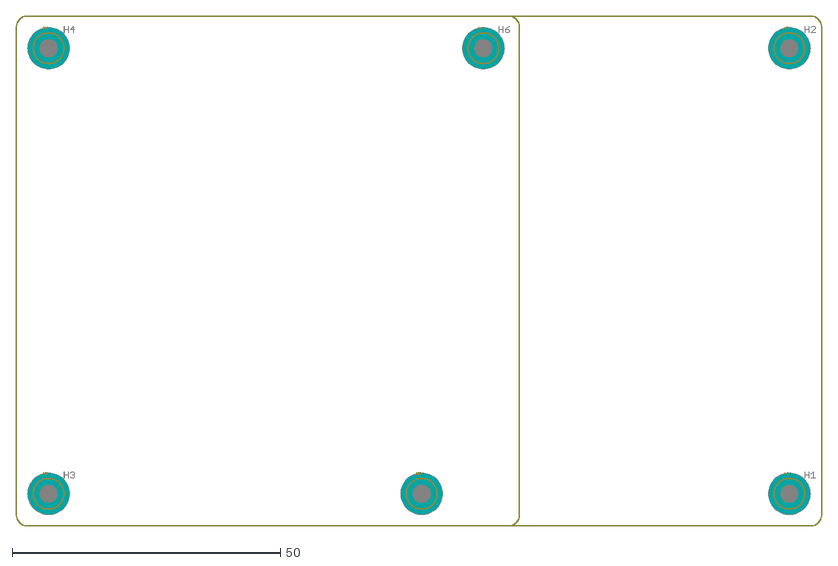
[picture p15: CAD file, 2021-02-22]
Board_Outlines/marionette_dxf.dxf
150.0 x 95.0

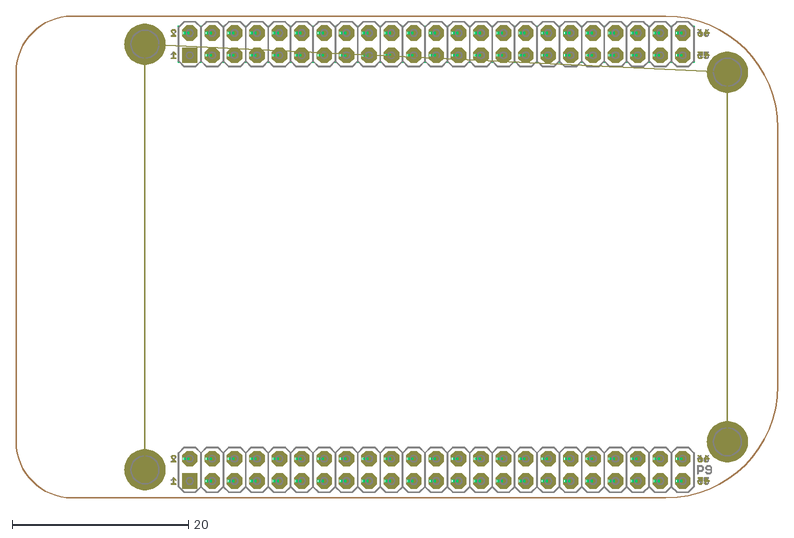
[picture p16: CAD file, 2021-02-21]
Board_Outlines/BeagleBone_Black_Wireless_Outline.dxf
86.4 x 54.6

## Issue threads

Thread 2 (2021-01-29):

AC Board - layout changes

jejor, 2021-01-29:
- Move the regulator above the fets/sov on the right side of the board; if possible move the redulator components under the nucleo add on, above CN7&CN10 while placing the battery terminal above the p-ch fets.
- Change sensor1-0 into vertical line along CN7.
- Reduce the overall width, increase height.
- Move info between CN7&CN10.

jejor, 2021-01-30:
waiting on ac board testing

jejor, 2021-01-31:
ac board testing done; nominal results. passed all test cases

jejor, 2021-01-31:
- [ ] Need to combine AC board and valve indicator board.
- [ ] Run AC processor off of USB from BB board
- [ ] Remove 12V-5V regulator
- [ ] Bare metal Nucleo down to board
- [ ] Add optoisolator to VBATT/12VPOE. Trigger VBATT on by 12V POE (power AC processor off of BB-USB)
- [ ] Combine tvs sensors from AC and Hall Effect sensors from Vi
- [ ] Keep 24V-3.3V regulator on Vi separate from AC processor

Closed 2021-03-25.

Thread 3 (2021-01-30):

All boards (AC, SFE, Vi, LOTO) replace all passives with oresat-rcl parts and compress boards.

jejor, 2021-01-30:

jejor, 2021-01-30:
- [ ] AC
- [ ] Vi
- [ ] LOTO
- [ ] SFE

Closed 2021-02-20.

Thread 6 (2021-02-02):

SFE Board Issues

jejor, 2021-02-02:
- [x] U$3 & U$8 need footprings changed to SSOP20
- [x] label unallocated NP resistors
- [x] allocate known sensors into next rev

jejor, 2021-02-20:
Change D31 & D27 to smaller package; see attribute DPN.

jejor, 2021-02-20:
Remove 5V regulator from board; add pinout for POE input board 5V regulator input.

jejor, 2021-02-20:
- [ ] Add Hall Effect inputs over DIO

jejor, 2021-02-20:
> [ ] Add Hall Effect inputs over DIO

Will need to test DIO lines on Marionette before we can verify function without changing firmware.

jejor, 2021-02-21:
- [ ] R75 part number wrong. Should be8.2k
- [ ] R1 pull down pressure should be 1% or better
- [ ] R1-r10 150ohm pull down change to 0.1%

Closed 2021-02-21.

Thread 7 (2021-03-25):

SFE Changes

jejor, 2021-03-25:
Change labels to consistent font/size. layout new components, complete attributes for new components.

jejor, 2021-04-03:
layout done. need to add tvs protection to 15 extra sensor lines

jejor, 2021-04-06:
added 14 extra sensor lines. one pin open to keep analog and digital lines separated.

Closed 2021-04-06.

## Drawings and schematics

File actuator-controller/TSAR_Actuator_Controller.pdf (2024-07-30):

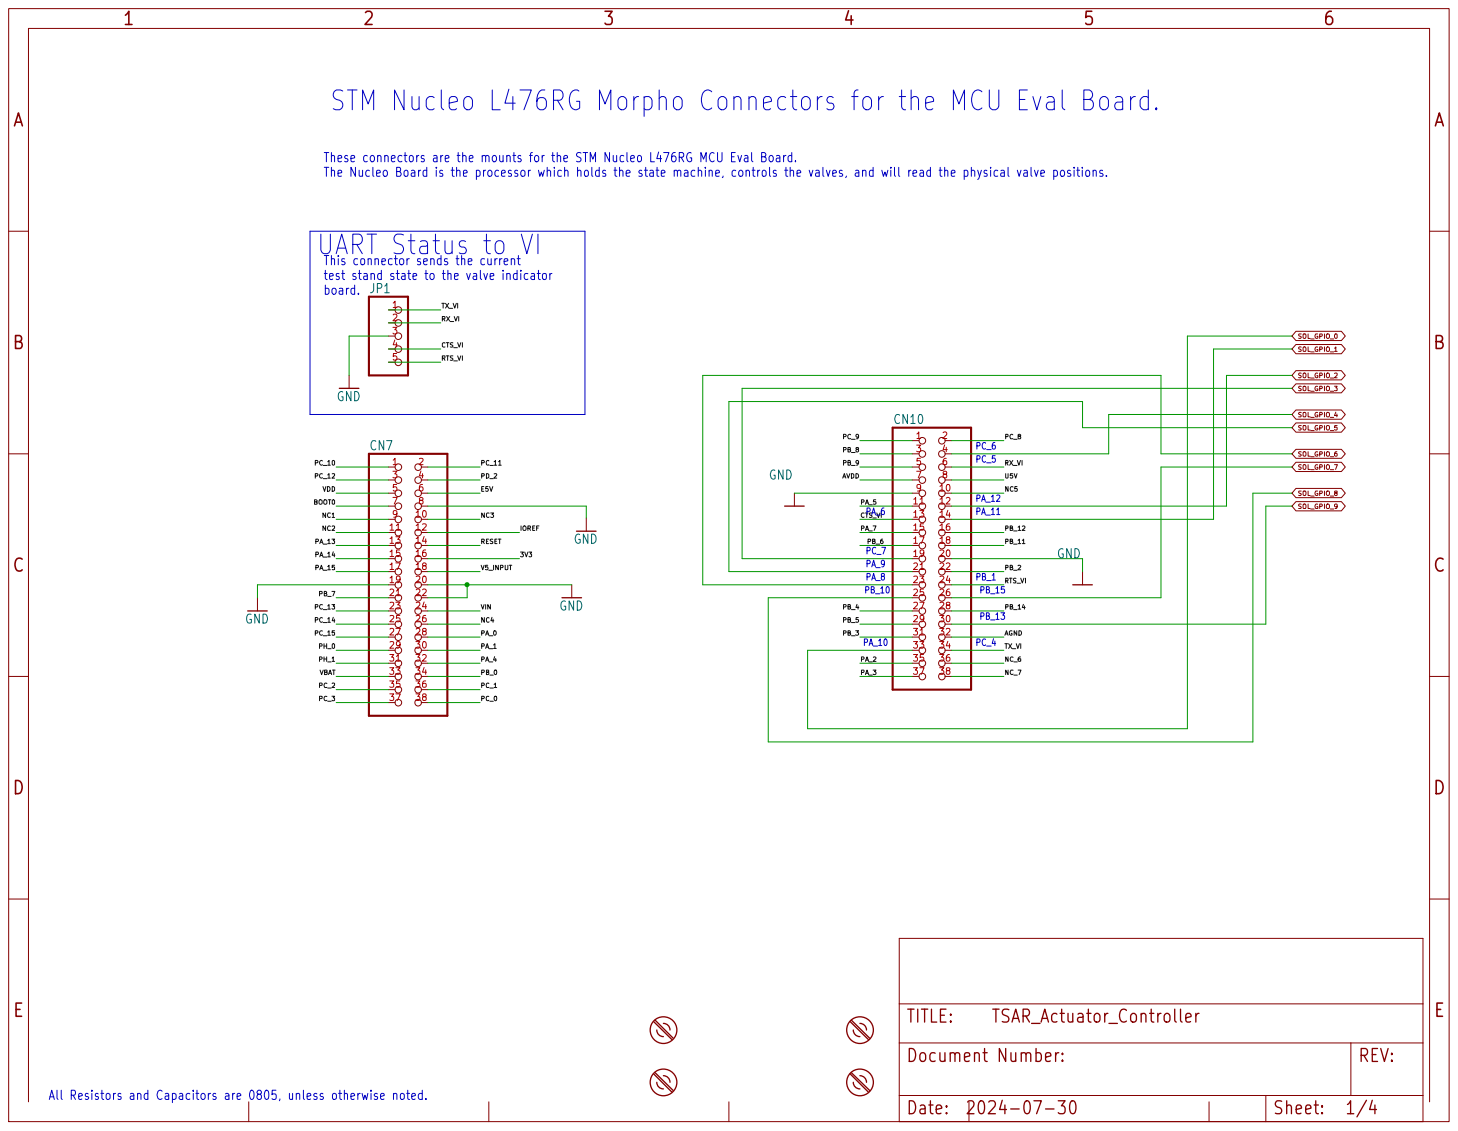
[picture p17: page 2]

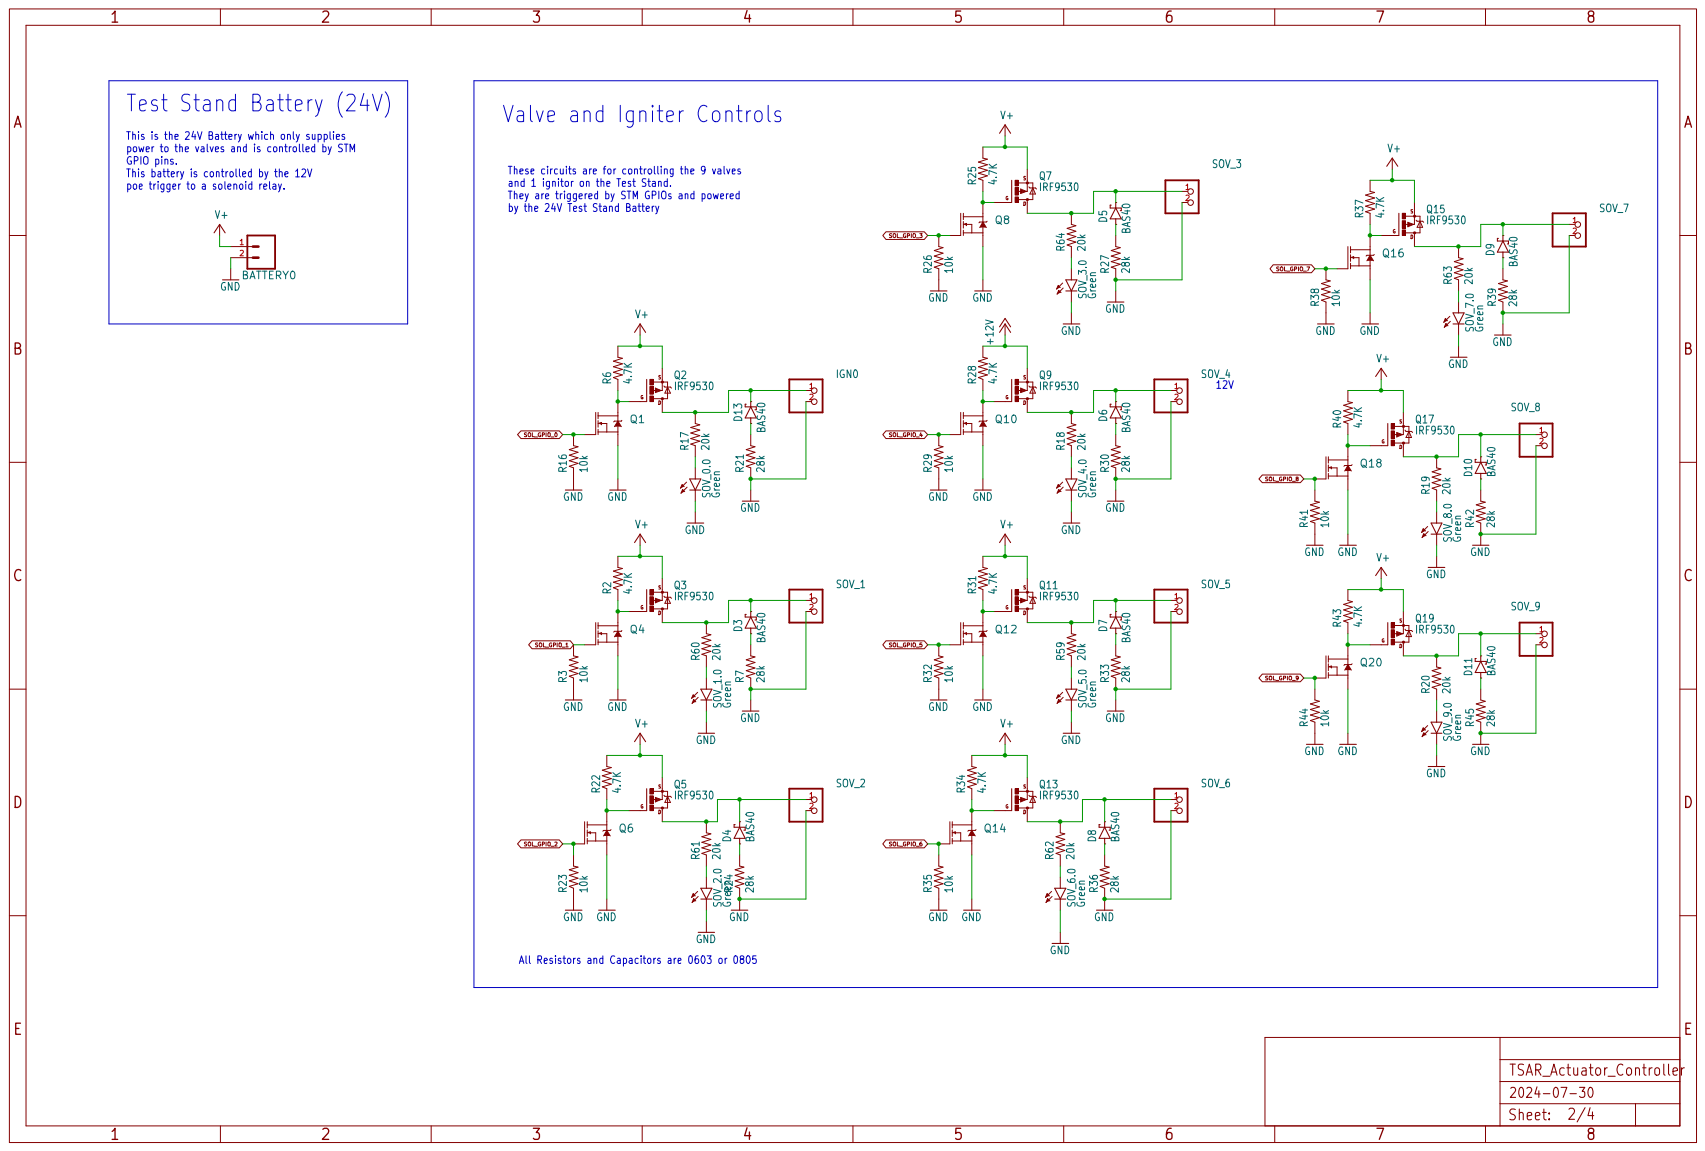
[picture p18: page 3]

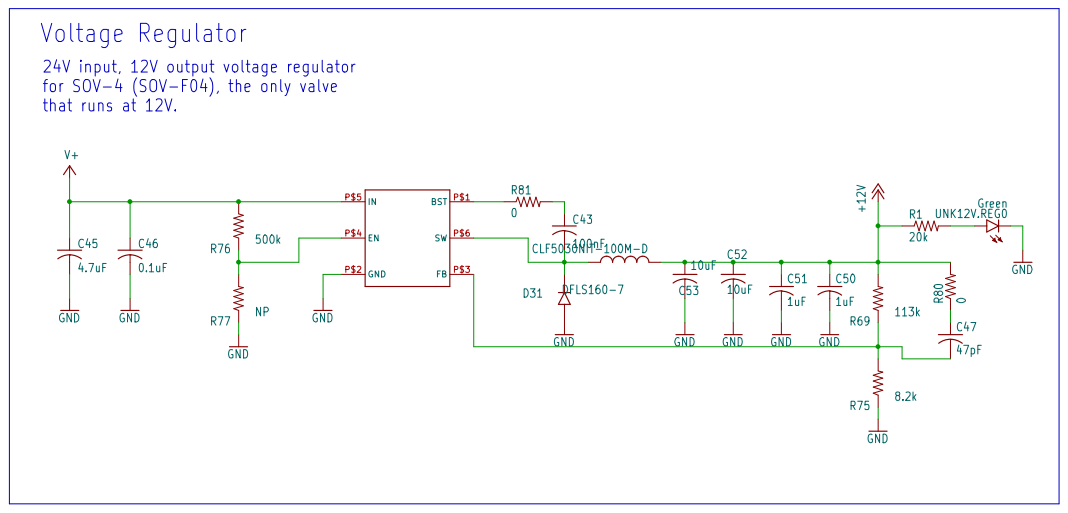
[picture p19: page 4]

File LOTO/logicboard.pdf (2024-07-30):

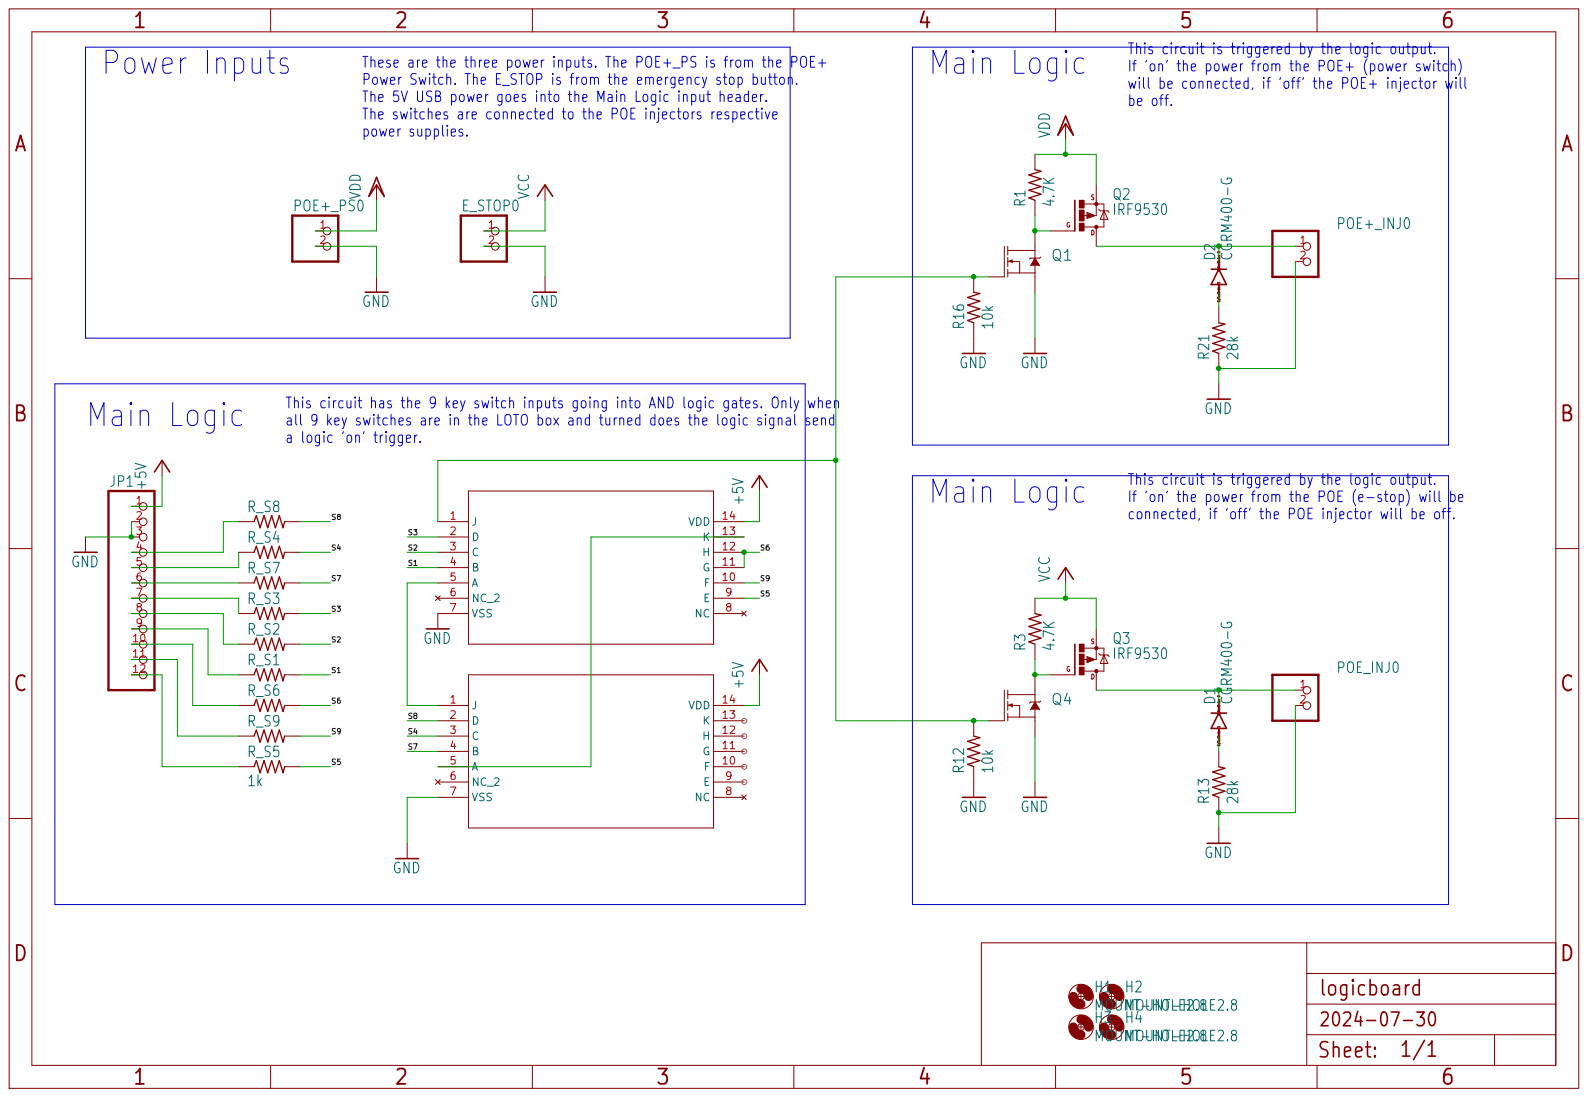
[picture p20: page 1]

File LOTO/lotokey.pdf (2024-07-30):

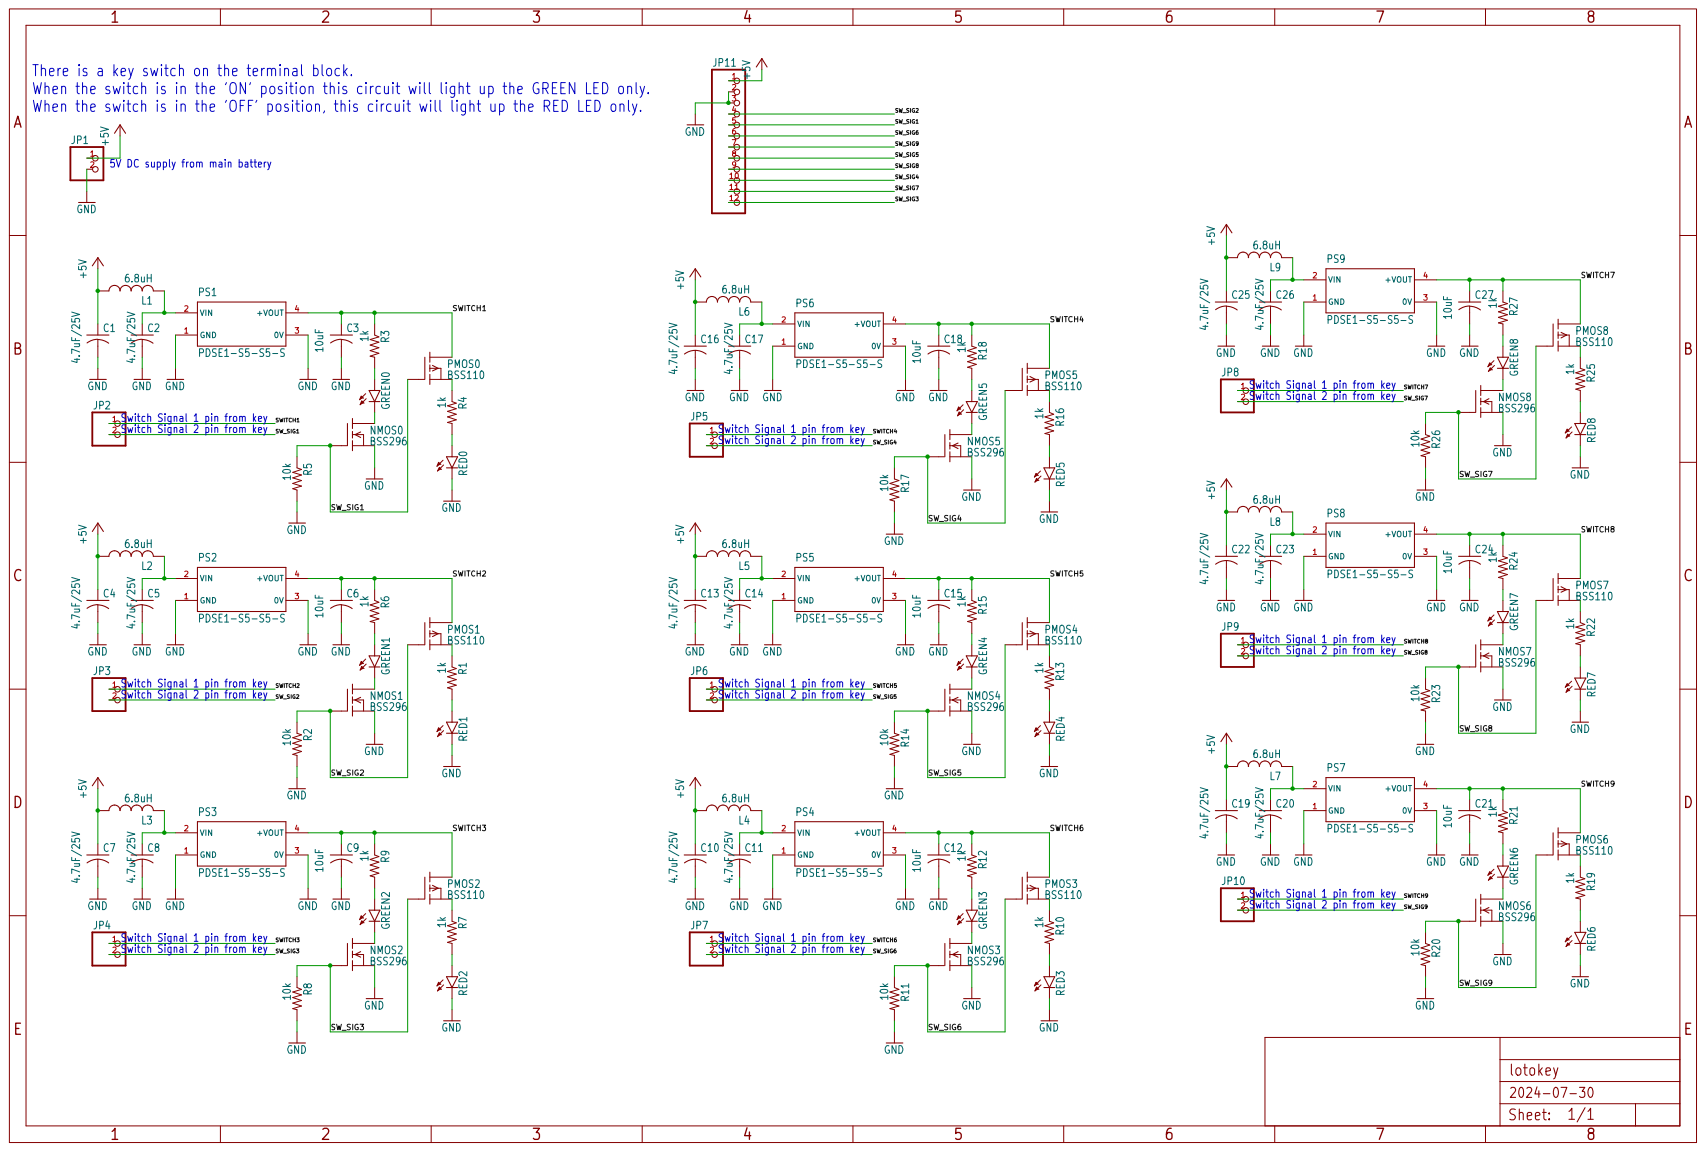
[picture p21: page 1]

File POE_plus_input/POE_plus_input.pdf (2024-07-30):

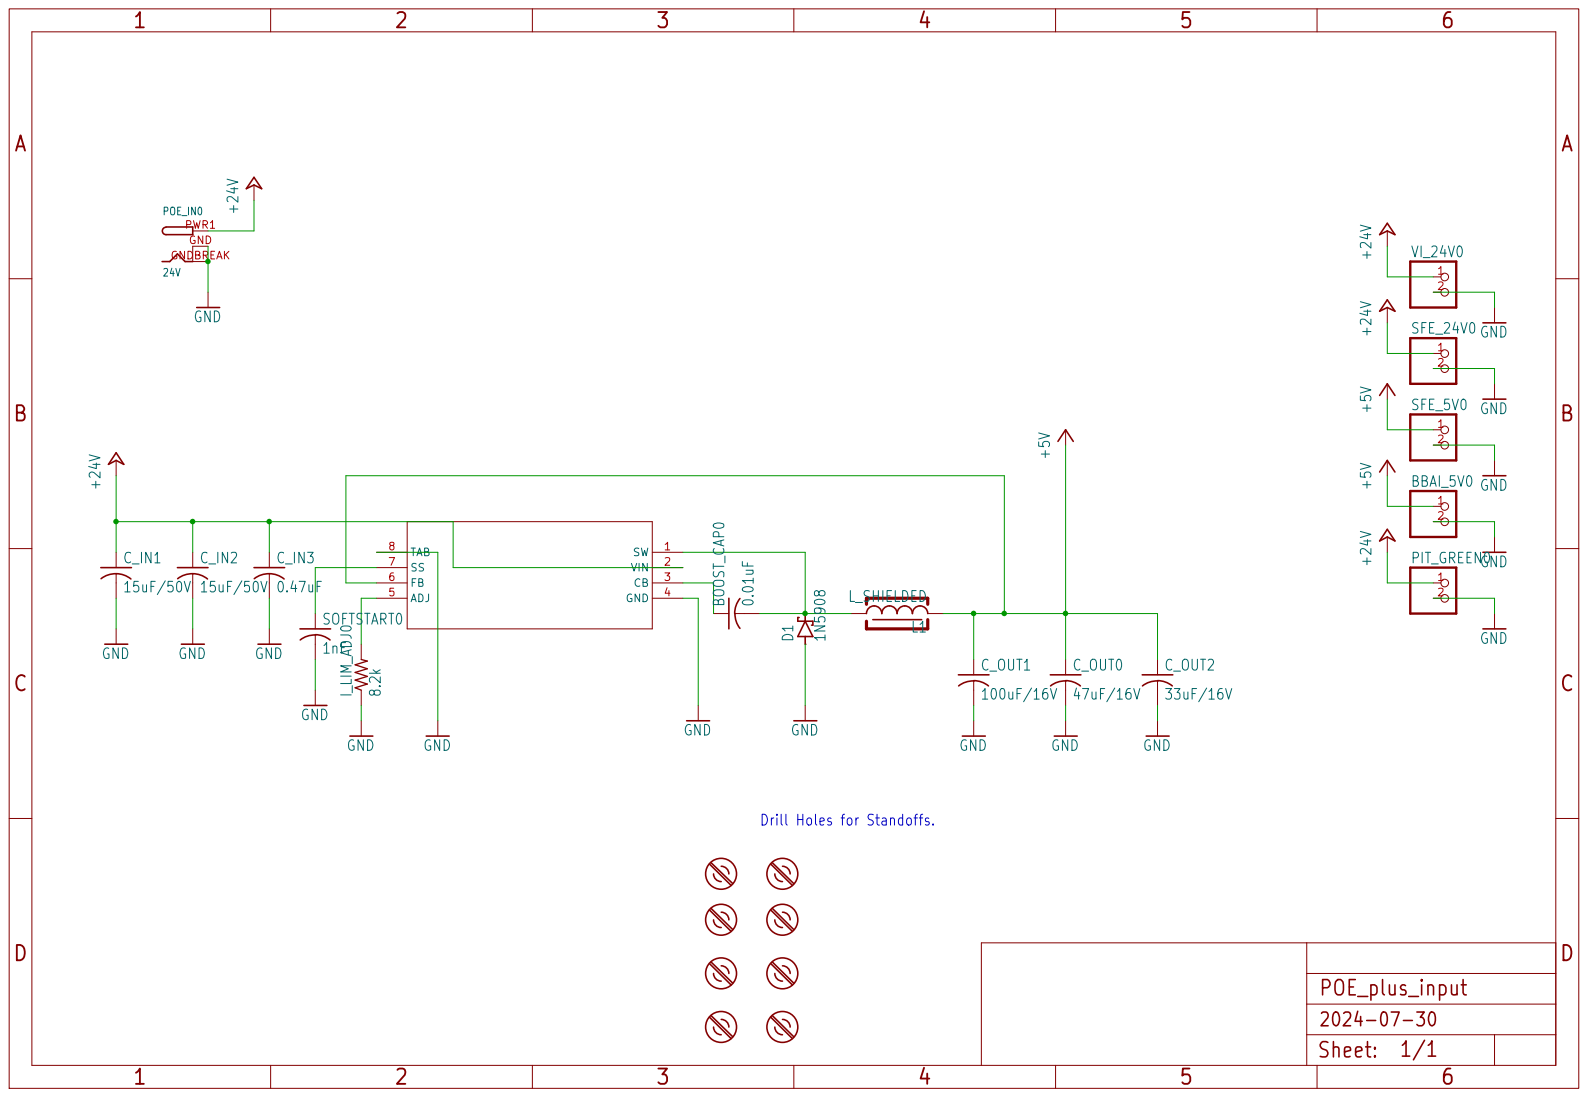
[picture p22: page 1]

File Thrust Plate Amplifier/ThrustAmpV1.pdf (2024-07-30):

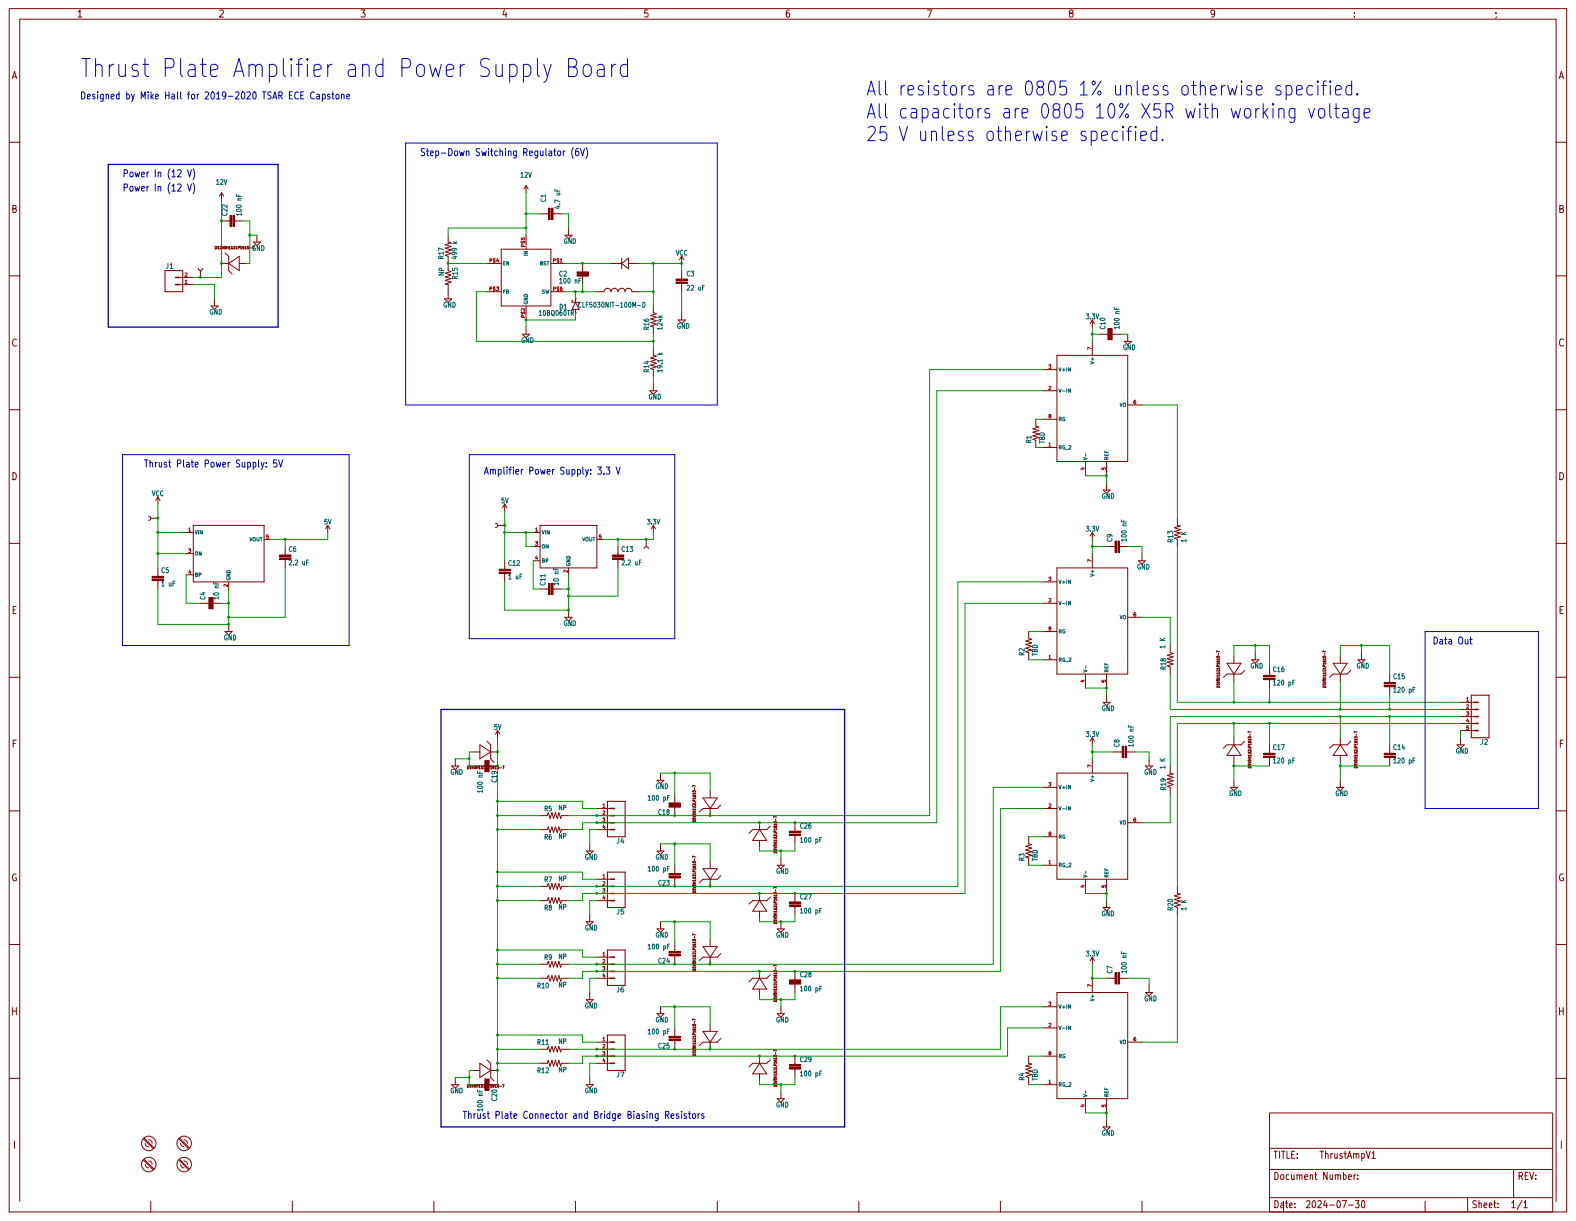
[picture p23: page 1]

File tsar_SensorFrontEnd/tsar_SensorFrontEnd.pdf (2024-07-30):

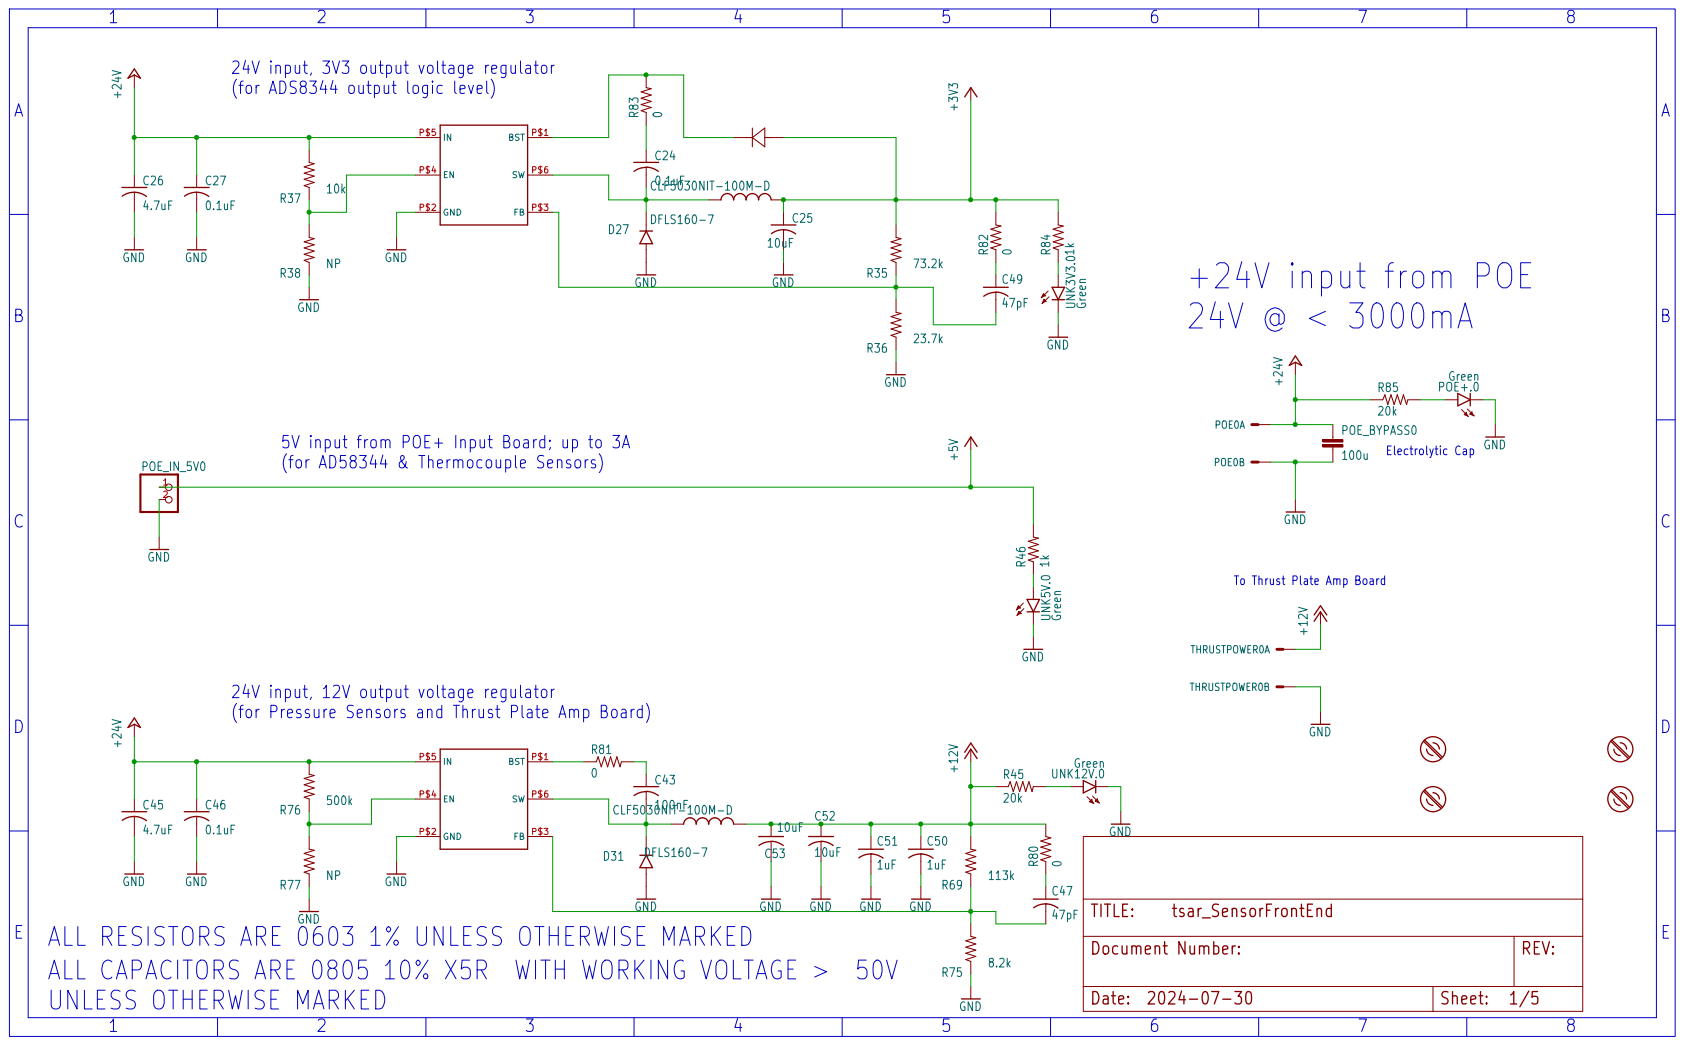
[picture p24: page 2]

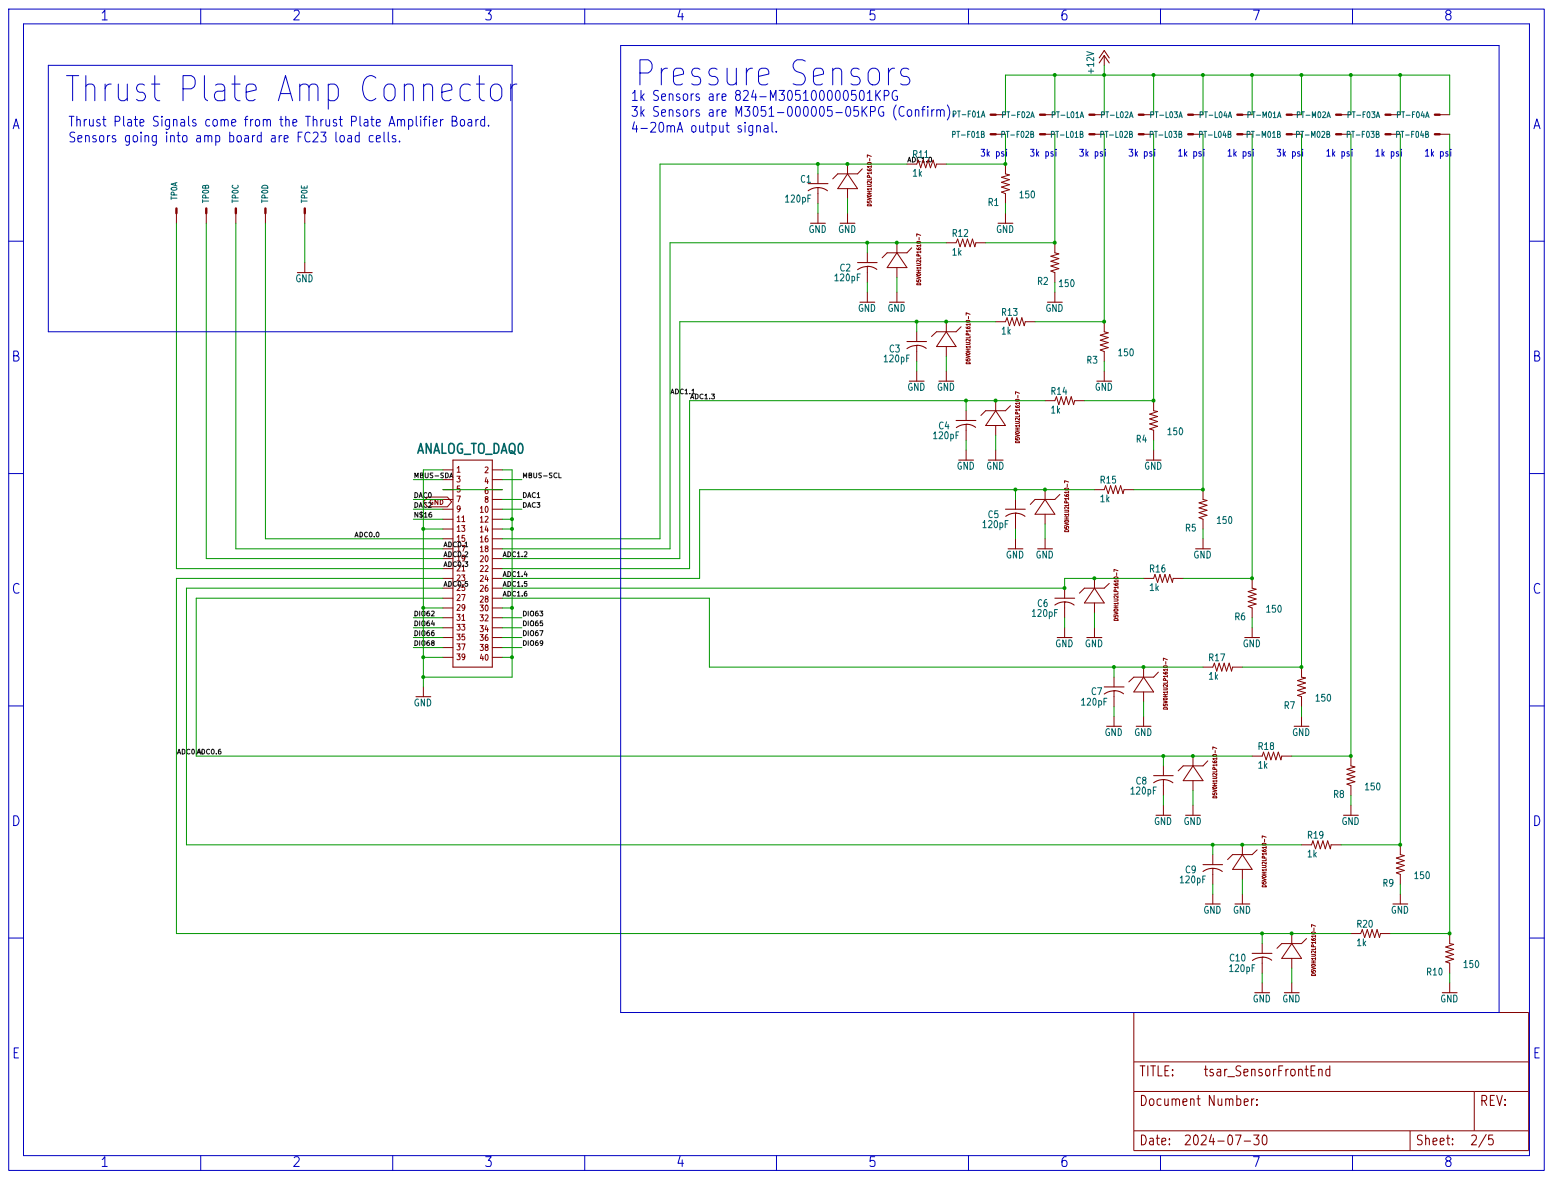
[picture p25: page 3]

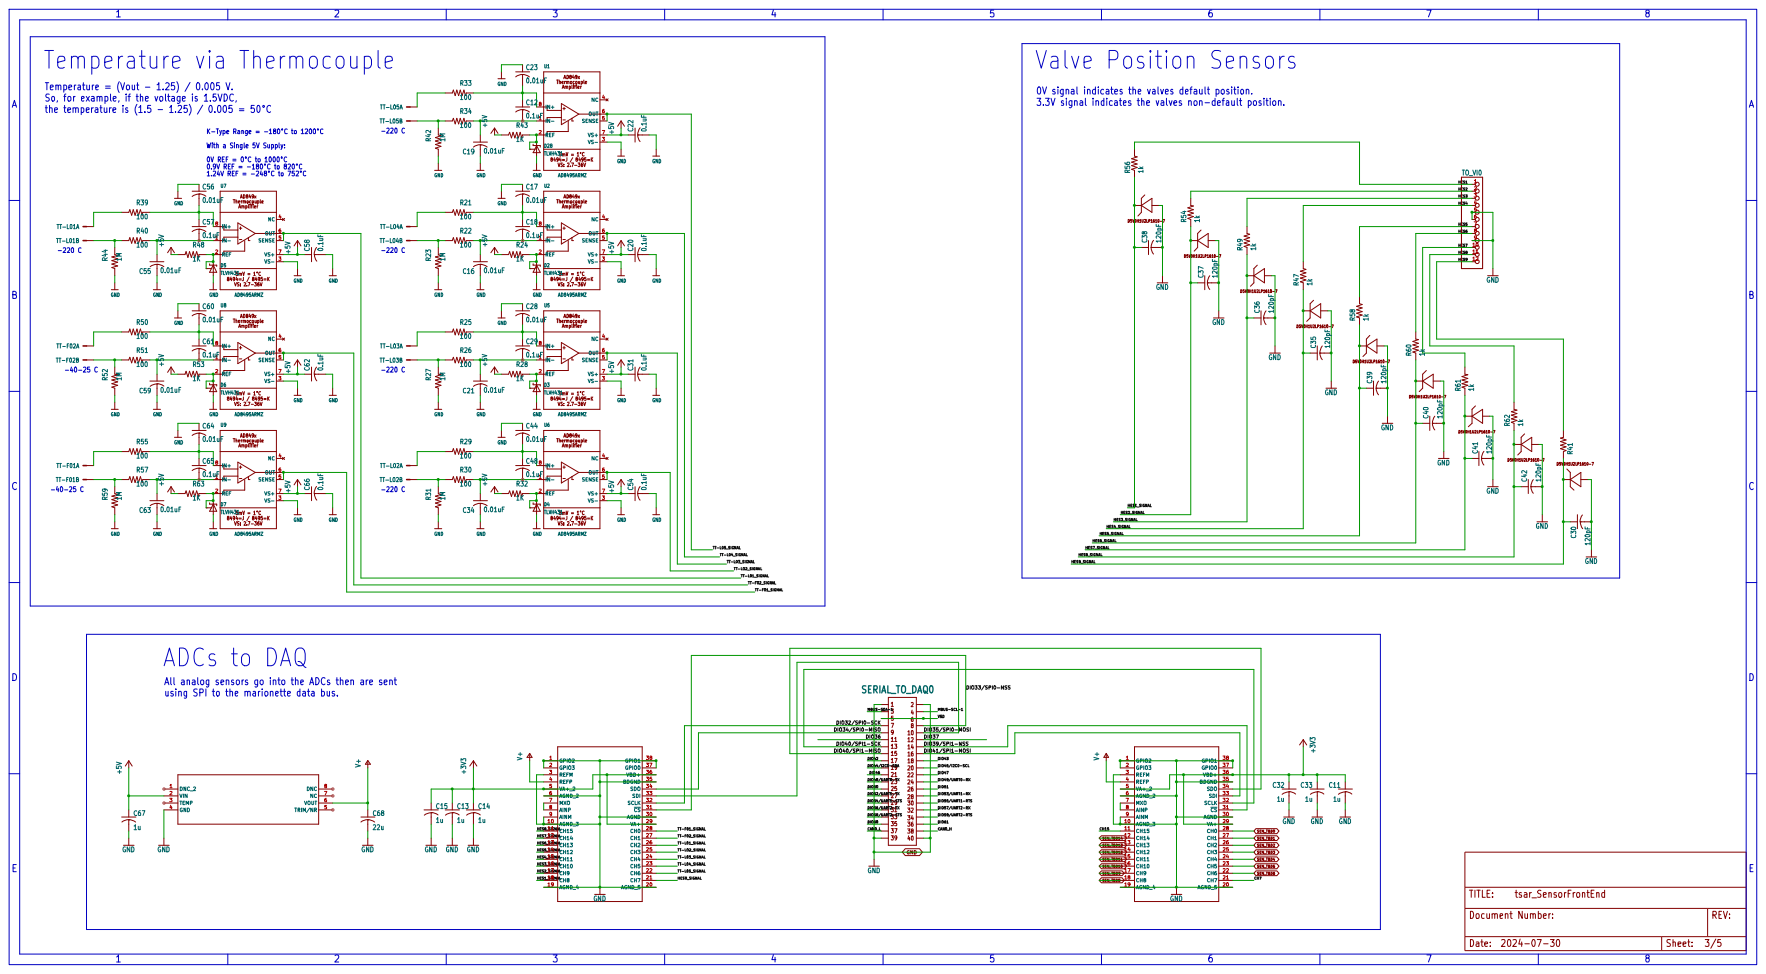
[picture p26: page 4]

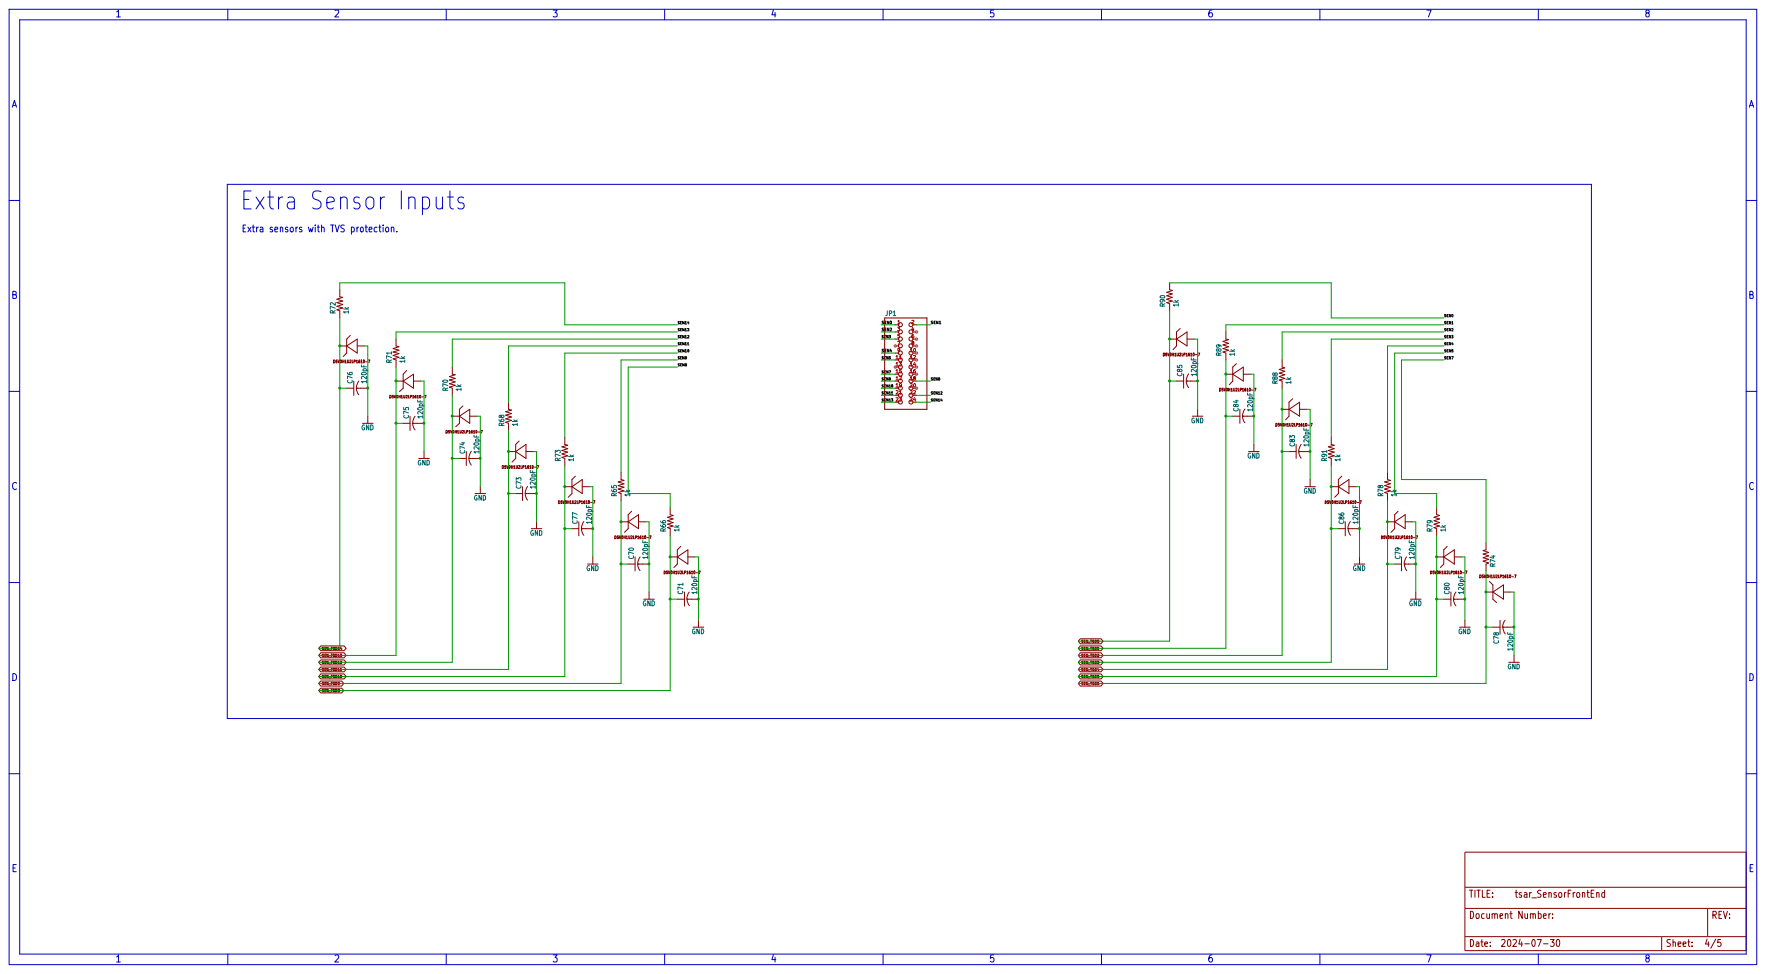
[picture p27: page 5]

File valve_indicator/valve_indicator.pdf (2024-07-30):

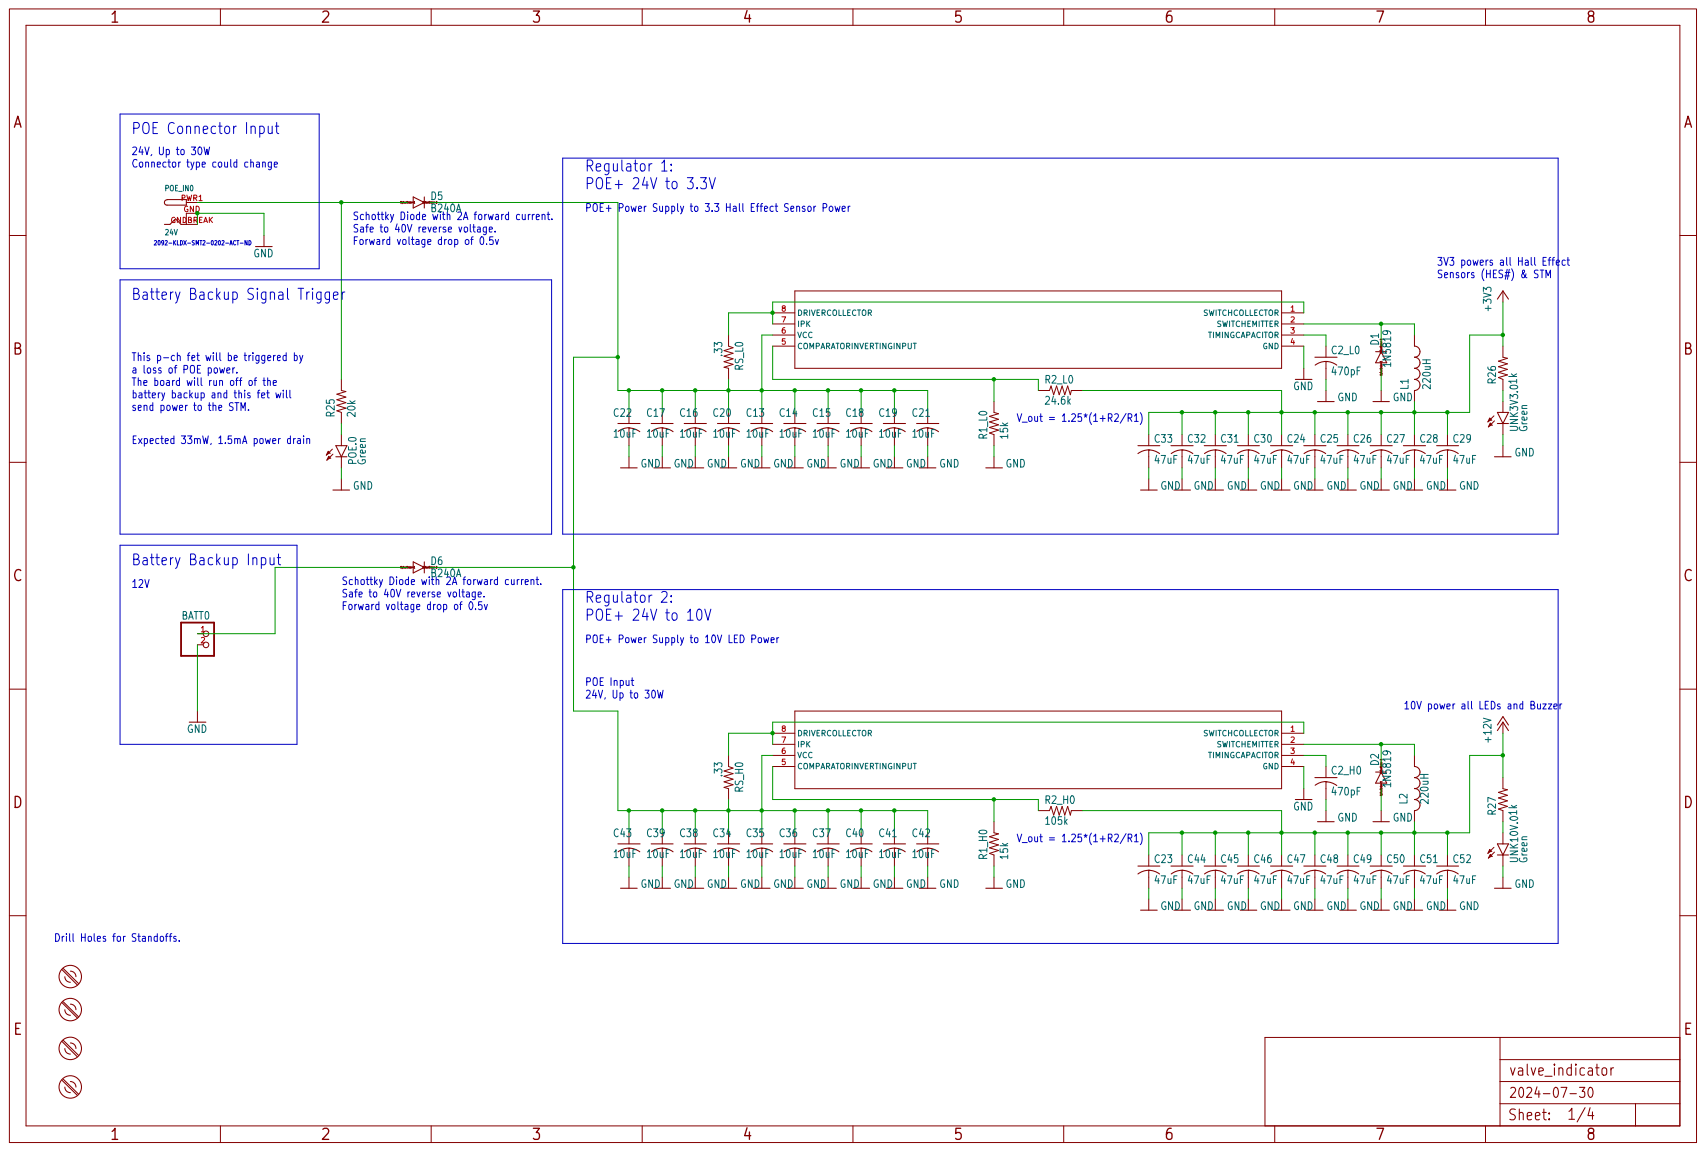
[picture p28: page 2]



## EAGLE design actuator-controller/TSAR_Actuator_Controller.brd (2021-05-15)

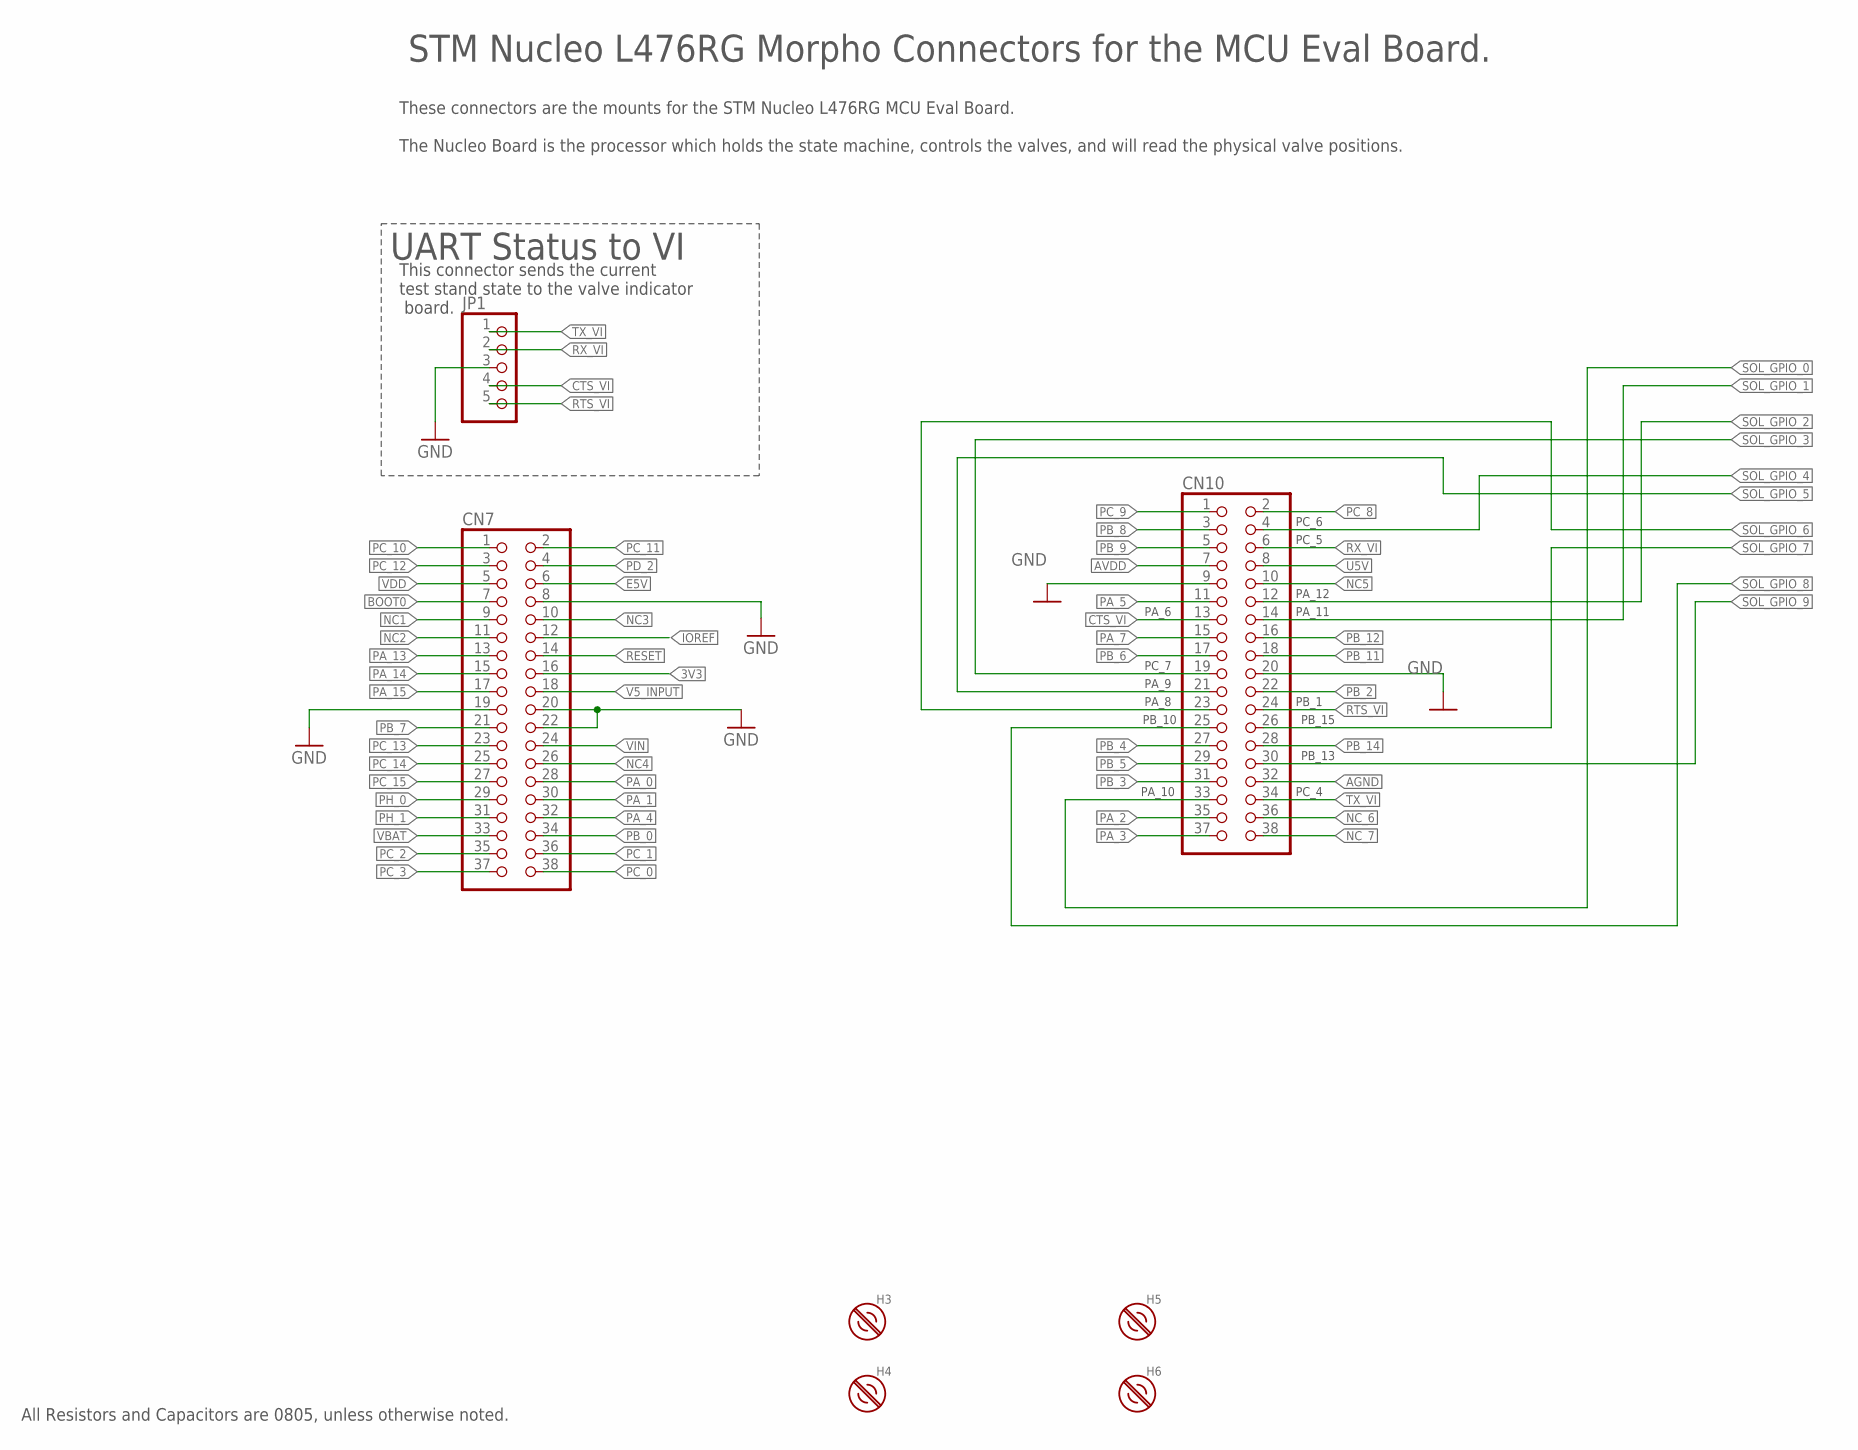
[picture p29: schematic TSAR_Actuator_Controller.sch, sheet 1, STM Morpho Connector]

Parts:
CN7, CN10: PINHD-2X19; 2X19; MPN PPPC192LFBN-RC
H3, H4, H5, H6: #4-BARE_MOUNTING_HOLE/.300; #4/.300-BARE+STD_NUT_OR_STAR_WASHER
JP1: PINHD-1X5; 1X05; MPN AWHW 10A-0202-T

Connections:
3V3: CN7.16
AGND: CN10.32
AVDD: CN10.7
BOOT0: CN7.7
CTS_VI: CN10.13, JP1.4
E5V: CN7.6
GND: CN7.8, CN7.19, CN7.20, CN7.22, CN10.9, CN10.20, JP1.3; also elsewhere on the board
IOREF: CN7.12
NC1: CN7.9
NC2: CN7.11
NC3: CN7.10
NC4: CN7.26
NC5: CN10.10
NC_6: CN10.36
NC_7: CN10.38
PA_0: CN7.28
PA_1: CN7.30
PA_2: CN10.35
PA_3: CN10.37
PA_4: CN7.32
PA_5: CN10.11
PA_7: CN10.15
PA_13: CN7.13
PA_14: CN7.15
PA_15: CN7.17
PB_0: CN7.34
PB_2: CN10.22
PB_3: CN10.31
PB_4: CN10.27
PB_5: CN10.29
PB_6: CN10.17
PB_7: CN7.21
PB_8: CN10.3
PB_9: CN10.5
PB_11: CN10.18
PB_12: CN10.16
PB_14: CN10.28
PC_0: CN7.38
PC_1: CN7.36
PC_2: CN7.35
PC_3: CN7.37
PC_8: CN10.2
PC_9: CN10.1
PC_10: CN7.1
PC_11: CN7.2
PC_12: CN7.3
PC_13: CN7.23
PC_14: CN7.25
PC_15: CN7.27
PD_2: CN7.4
PH_0: CN7.29
PH_1: CN7.31
RESET: CN7.14
RTS_VI: CN10.24, JP1.5
RX_VI: CN10.6, JP1.2
SOL_GPIO_0: CN10.33; also elsewhere on the board
SOL_GPIO_1: CN10.14; also elsewhere on the board
SOL_GPIO_2: CN10.12; also elsewhere on the board
SOL_GPIO_3: CN10.19; also elsewhere on the board
SOL_GPIO_4: CN10.4; also elsewhere on the board
SOL_GPIO_5: CN10.21; also elsewhere on the board
SOL_GPIO_6: CN10.23; also elsewhere on the board
SOL_GPIO_7: CN10.26; also elsewhere on the board
SOL_GPIO_8: CN10.25; also elsewhere on the board
SOL_GPIO_9: CN10.30; also elsewhere on the board
TX_VI: CN10.34, JP1.1
U5V: CN10.8
V5_INPUT: CN7.18
VBAT: CN7.33
VDD: CN7.5
VIN: CN7.24

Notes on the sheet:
STM Nucleo L476RG Morpho Connectors for the MCU Eval Board.
All Resistors and Capacitors are 0805, unless otherwise noted.
These connectors are the mounts for the STM Nucleo L476RG MCU Eval Board. The Nucleo Board is the processor which holds the state machine, controls the valves, and will read the physical valve positions.
PC_7
PA_9
PA_8
PB_10
PA_10
PC_6
PB_15
PB_13
This connector sends the current test stand state to the valve indicator board.
UART Status to VI
PA_6
PC_5
PB_1
PC_4
PA_11
PA_12

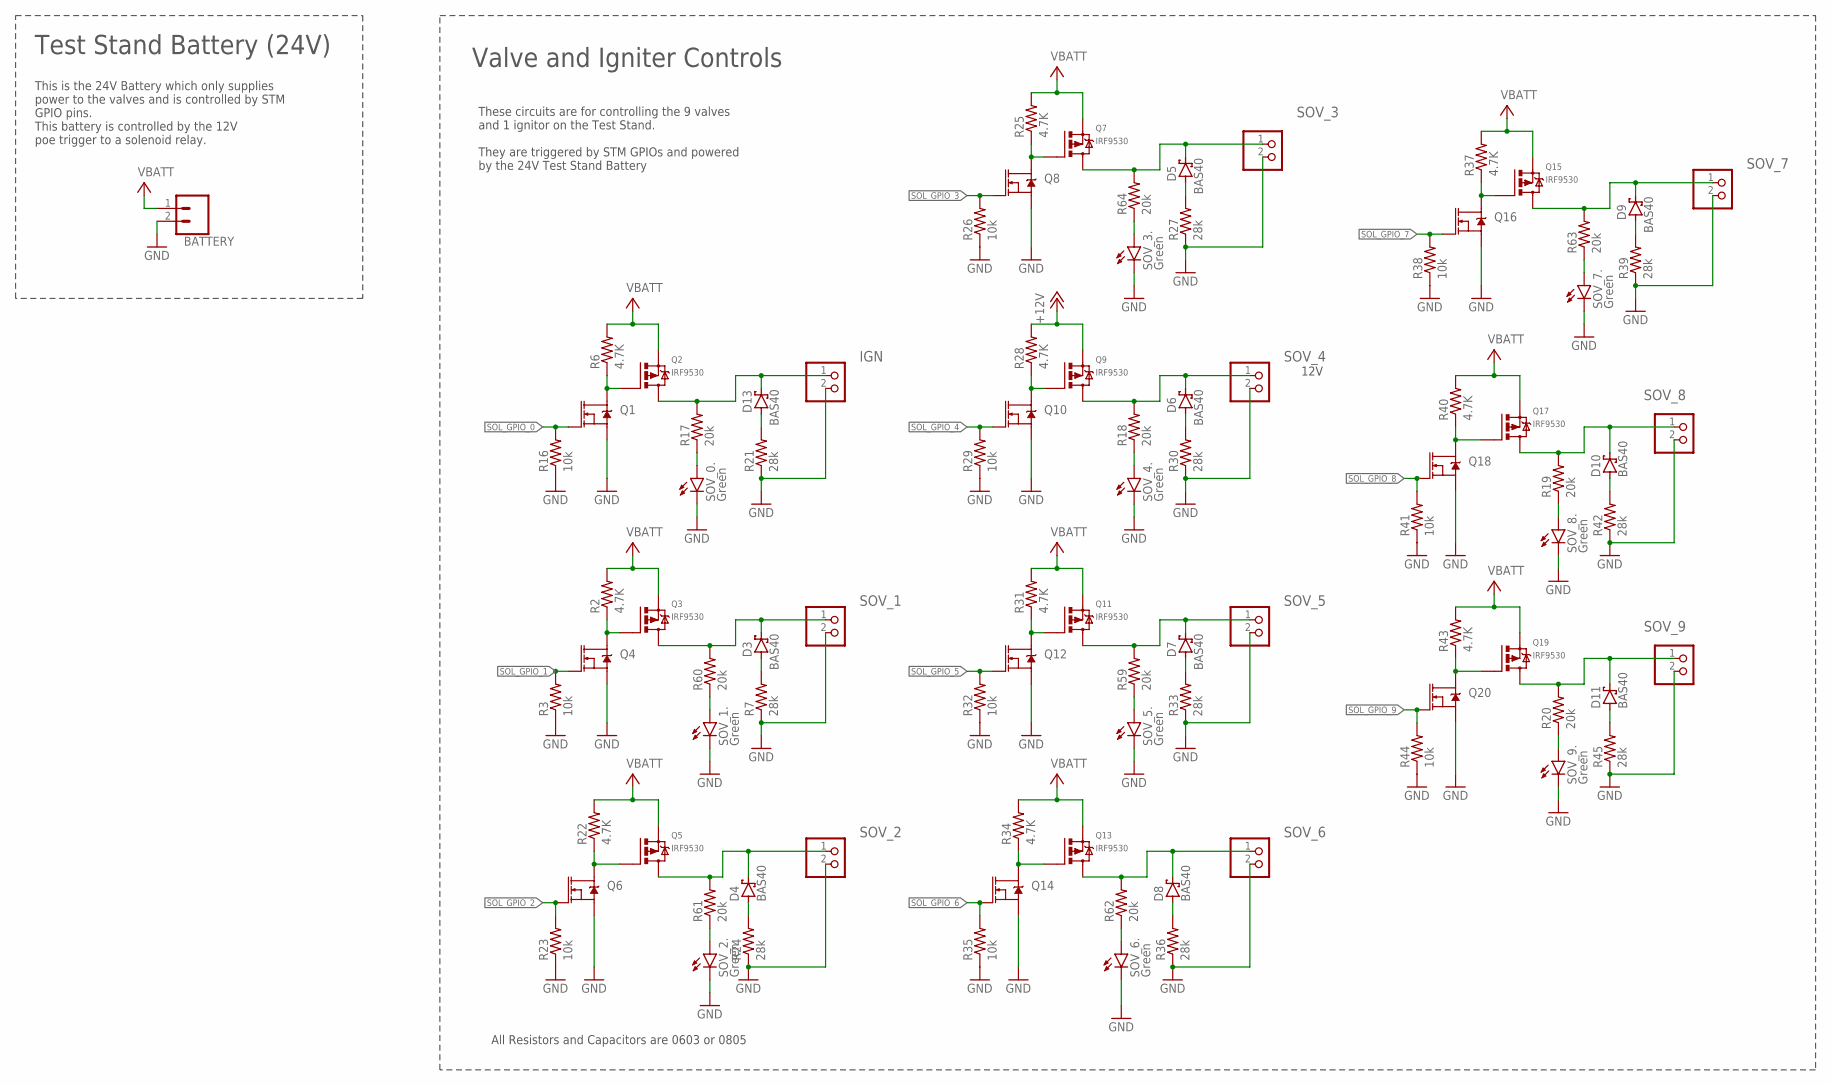
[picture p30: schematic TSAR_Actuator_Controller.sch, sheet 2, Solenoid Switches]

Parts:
BATTERY: CONN_02PTH4; 1X02_XTRA_BIG; MPN 282837-2
D3, D4, D5, D6, D7, D8, D9, D10, D11, D13: BAS40; SOT23; MPN CMPSH1-4 TR PBFREE
IGN: PINHD-1X2; 1X02; MPN 0022232021
Q1, Q4, Q6, Q8, Q10, Q12, Q14, Q16, Q18, Q20: 220mA/50V/3.5Ω; SOT23-3; MPN BSS138P,215
Q2, Q3, Q5, Q7, Q9, Q11, Q13, Q15, Q17, Q19: IRF9530; TO220BV; MPN IRF9530NPBF
R2, R6, R22, R25, R28, R31, R34, R37, R40, R43: 4.7K; .0805-A-NOSILK; MPN RC0805FR-074K7L
R3, R16, R23, R26, R29, R32, R35, R38, R41, R44: 10k; .0805-A-NOSILK; MPN RC0805FR-0710KL
R7, R21, R24, R27, R30, R33, R36, R39, R42, R45: 28k; .0805-A-NOSILK; MPN RMCF0805FT28K0
R17, R18, R19, R20, R59, R60, R61, R62, R63, R64: 20k; .0603-A-NOSILK; MPN ESR03EZPJ203
SOV_0., SOV_1., SOV_2., SOV_3., SOV_4., SOV_5., SOV_6., SOV_7., SOV_8., SOV_9.: Green; CHIP-LED0603; MPN 5988070107F
SOV_1, SOV_2, SOV_3, SOV_4, SOV_5, SOV_6, SOV_7, SOV_8, SOV_9: PINHD-1X2; 1X02; MPN 0022232021

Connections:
+12V: Q9.S, R28.2; also elsewhere on the board
GND: BATTERY.2, IGN.2, Q1.2 (S), Q4.2 (S), Q6.2 (S), Q8.2 (S), Q10.2 (S), Q12.2 (S), Q14.2 (S), Q16.2 (S), Q18.2 (S), Q20.2 (S), R3.1, R7.1, R16.1, R21.1, R23.1, R24.1, R26.1, R27.1, R29.1, R30.1, R32.1, R33.1, R35.1, R36.1, R38.1, R39.1, R41.1, R42.1, R44.1, R45.1, SOV_0..C, SOV_1.2, SOV_1..C, SOV_2.2, SOV_2..C, SOV_3.2, SOV_3..C, SOV_4.2, SOV_4..C, SOV_5.2, SOV_5..C, SOV_6.2, SOV_6..C, SOV_7.2, SOV_7..C, SOV_8.2, SOV_8..C, SOV_9.2, SOV_9..C; also elsewhere on the board
unnamed: Q1.3 (D), Q2.G, R6.1
unnamed: R17.1, SOV_0..A
unnamed: R18.1, SOV_4..A
unnamed: R19.1, SOV_8..A
unnamed: R20.1, SOV_9..A
unnamed: R59.1, SOV_5..A
unnamed: R60.1, SOV_1..A
unnamed: R61.1, SOV_2..A
unnamed: R62.1, SOV_6..A
unnamed: R63.1, SOV_7..A
unnamed: R64.1, SOV_3..A
unnamed: D3.1 (A), R7.2
unnamed: Q3.G, Q4.3 (D), R2.1
unnamed: D4.1 (A), R24.2
unnamed: Q5.G, Q6.3 (D), R22.1
unnamed: D5.1 (A), R27.2
unnamed: Q7.G, Q8.3 (D), R25.1
unnamed: D6.1 (A), R30.2
unnamed: Q9.G, Q10.3 (D), R28.1
unnamed: D7.1 (A), R33.2
unnamed: Q11.G, Q12.3 (D), R31.1
unnamed: D8.1 (A), R36.2
unnamed: Q13.G, Q14.3 (D), R34.1
unnamed: D9.1 (A), R39.2
unnamed: Q15.G, Q16.3 (D), R37.1
unnamed: D10.1 (A), R42.2
unnamed: Q17.G, Q18.3 (D), R40.1
unnamed: D11.1 (A), R45.2
unnamed: Q19.G, Q20.3 (D), R43.1
unnamed: D13.1 (A), R21.2
SOL_GPIO_0: Q1.1 (G), R16.2; also elsewhere on the board
SOL_GPIO_1: Q4.1 (G), R3.2; also elsewhere on the board
SOL_GPIO_2: Q6.1 (G), R23.2; also elsewhere on the board
SOL_GPIO_3: Q8.1 (G), R26.2; also elsewhere on the board
SOL_GPIO_4: Q10.1 (G), R29.2; also elsewhere on the board
SOL_GPIO_5: Q12.1 (G), R32.2; also elsewhere on the board
SOL_GPIO_6: Q14.1 (G), R35.2; also elsewhere on the board
SOL_GPIO_7: Q16.1 (G), R38.2; also elsewhere on the board
SOL_GPIO_8: Q18.1 (G), R41.2; also elsewhere on the board
SOL_GPIO_9: Q20.1 (G), R44.2; also elsewhere on the board
SOL_GPIO_10: D13.3 (C), IGN.1, Q2.D, R17.2
SOL_GPIO_11: D3.3 (C), Q3.D, R60.2, SOV_1.1
SOL_GPIO_12: D4.3 (C), Q5.D, R61.2, SOV_2.1
SOL_GPIO_13: D5.3 (C), Q7.D, R64.2, SOV_3.1
SOL_GPIO_14: D6.3 (C), Q9.D, R18.2, SOV_4.1
SOL_GPIO_15: D7.3 (C), Q11.D, R59.2, SOV_5.1
SOL_GPIO_16: D8.3 (C), Q13.D, R62.2, SOV_6.1
SOL_GPIO_17: D9.3 (C), Q15.D, R63.2, SOV_7.1
SOL_GPIO_18: D10.3 (C), Q17.D, R19.2, SOV_8.1
SOL_GPIO_19: D11.3 (C), Q19.D, R20.2, SOV_9.1
VBATT: BATTERY.1, Q2.S, Q3.S, Q5.S, Q7.S, Q11.S, Q13.S, Q15.S, Q17.S, Q19.S, R2.2, R6.2, R22.2, R25.2, R31.2, R34.2, R37.2, R40.2, R43.2; also elsewhere on the board

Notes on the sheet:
All Resistors and Capacitors are 0603 or 0805
Valve and Igniter Controls
These circuits are for controlling the 9 valves and 1 ignitor on the Test Stand. They are triggered by STM GPIOs and powered by the 24V Test Stand Battery
This is the 24V Battery which only supplies power to the valves and is controlled by STM GPIO pins. This battery is controlled by the 12V poe trigger to a solenoid relay.
Test Stand Battery (24V)
12V

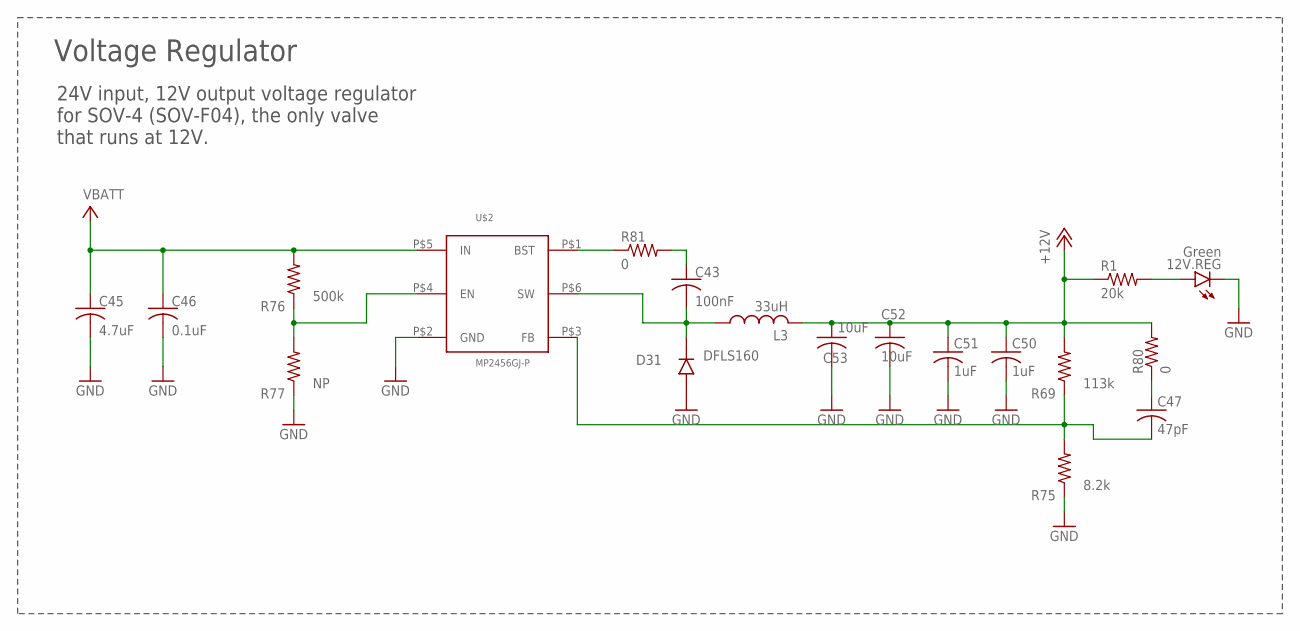
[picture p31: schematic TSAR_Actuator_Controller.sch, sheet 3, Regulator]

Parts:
12V.REG: Green; CHIP-LED0603; MPN 5988070107F
C43: 100nF; C0603K; MPN CL10B104KB8NNNL
C45: 4.7uF; C0805K; MPN CL21A475KBQNNNE
C46: 0.1uF; C0603K; MPN CL10B104KB8NNNL
C47: 47pF; C0603K; MPN C1608C0G1H470J080AA
C50, C51: 1uF; C0603K; MPN CL10A105KB8NNNC
C52, C53: 10uF; C1206K; MPN CL31A106MBHNNNE
D31: DFLS160; POWERDI-123; MPN DFLS160-7
L3: 33uH; 0.209"LX0.197"W(5.30MMX5.00MM); MPN PM4340.333NLT
R1: 20k; .0603-A-NOSILK; MPN ERJ-PA3J203V
R69: 113k; .0805-A-NOSILK; MPN RK73H2ATTD1133F
R75: 8.2k; .0805-A-NOSILK; MPN RK73H2ATTD8201F
R76: 500k; 1206-A; MPN CRMA1206AF500KFKEF
R77: NP; .0805-A-NOSILK
R80, R81: 0; .0603-A-NOSILK; MPN RCS06030000Z0EA
U$2: MP2456GJ-P; SOT6; MPN MP2456GJ-P

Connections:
+12V: C50.1, C51.1, C52.1, C53.1, L3.2, R1.1, R69.2, R80.2; also elsewhere on the board
FLY3: C43.2, D31.C, L3.1, U$2.P$6 (SW)
GND: 12V.REG.C, C45.2, C46.2, C50.2, C51.2, C52.2, C53.2, D31.A, R75.1, R77.1, U$2.P$2 (GND); also elsewhere on the board
unnamed: 12V.REG.A, R1.2
unnamed: C43.1, R81.2
unnamed: C47.2, R69.1, R75.2, U$2.P$3 (FB)
unnamed: R76.1, R77.2, U$2.P$4 (EN)
unnamed: C47.1, R80.1
unnamed: R81.1, U$2.P$1 (BST)
VBATT: C45.1, C46.1, R76.2, U$2.P$5 (IN); also elsewhere on the board

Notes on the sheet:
24V input, 12V output voltage regulator for SOV-4 (SOV-F04), the only valve that runs at 12V.
Voltage Regulator

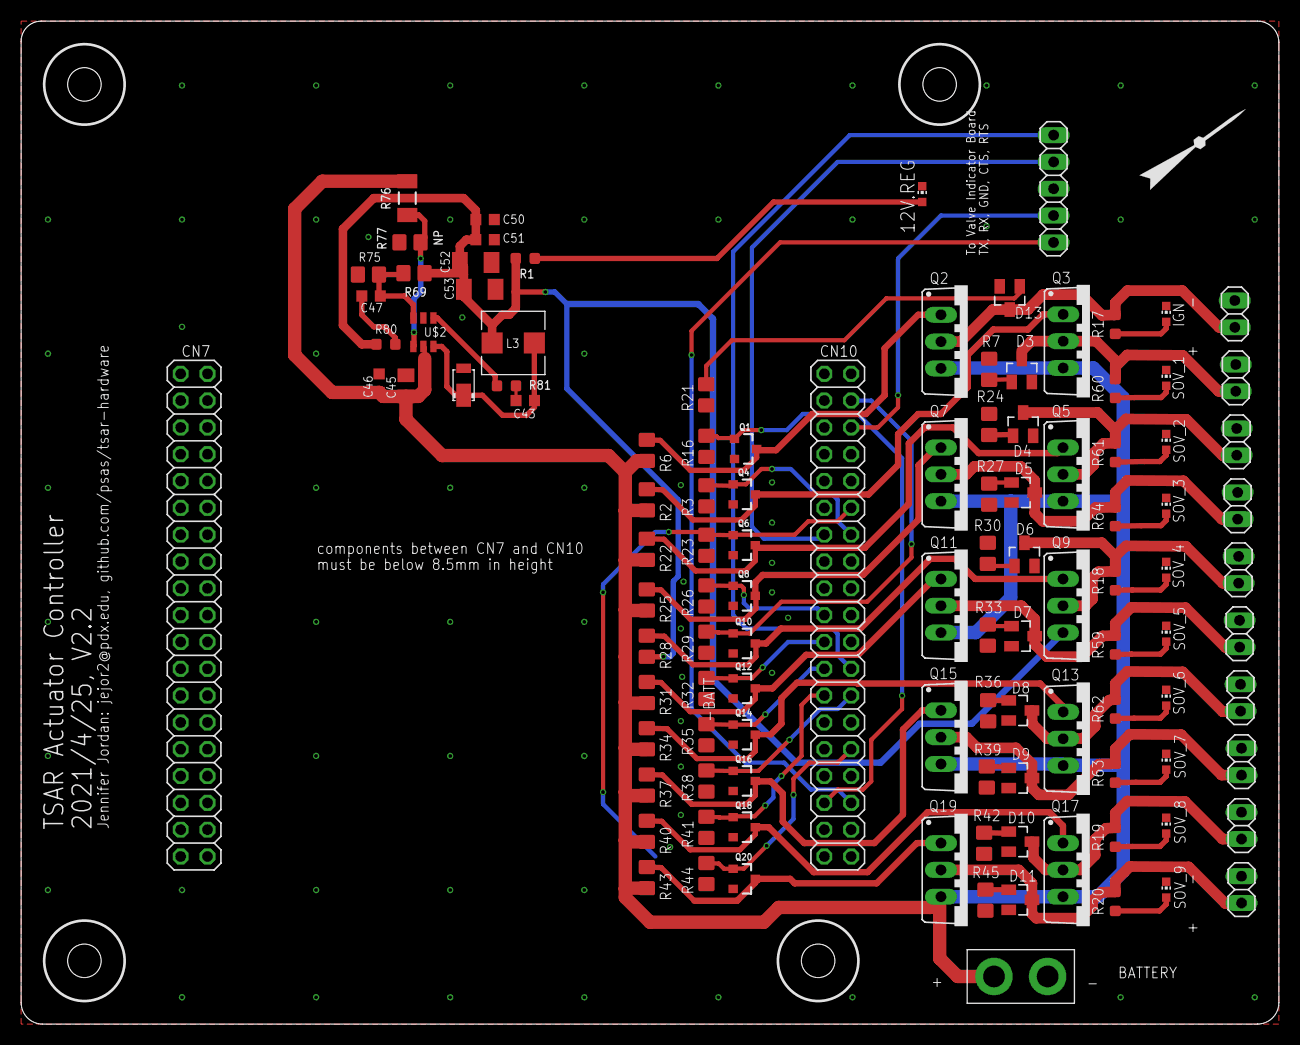
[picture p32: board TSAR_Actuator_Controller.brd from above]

Board: 2 copper layers, 119.1 x 95.0 mm, 118 parts (0 on the bottom side), 64 nets.

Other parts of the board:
U$1: PSAS_LOGO_10X10

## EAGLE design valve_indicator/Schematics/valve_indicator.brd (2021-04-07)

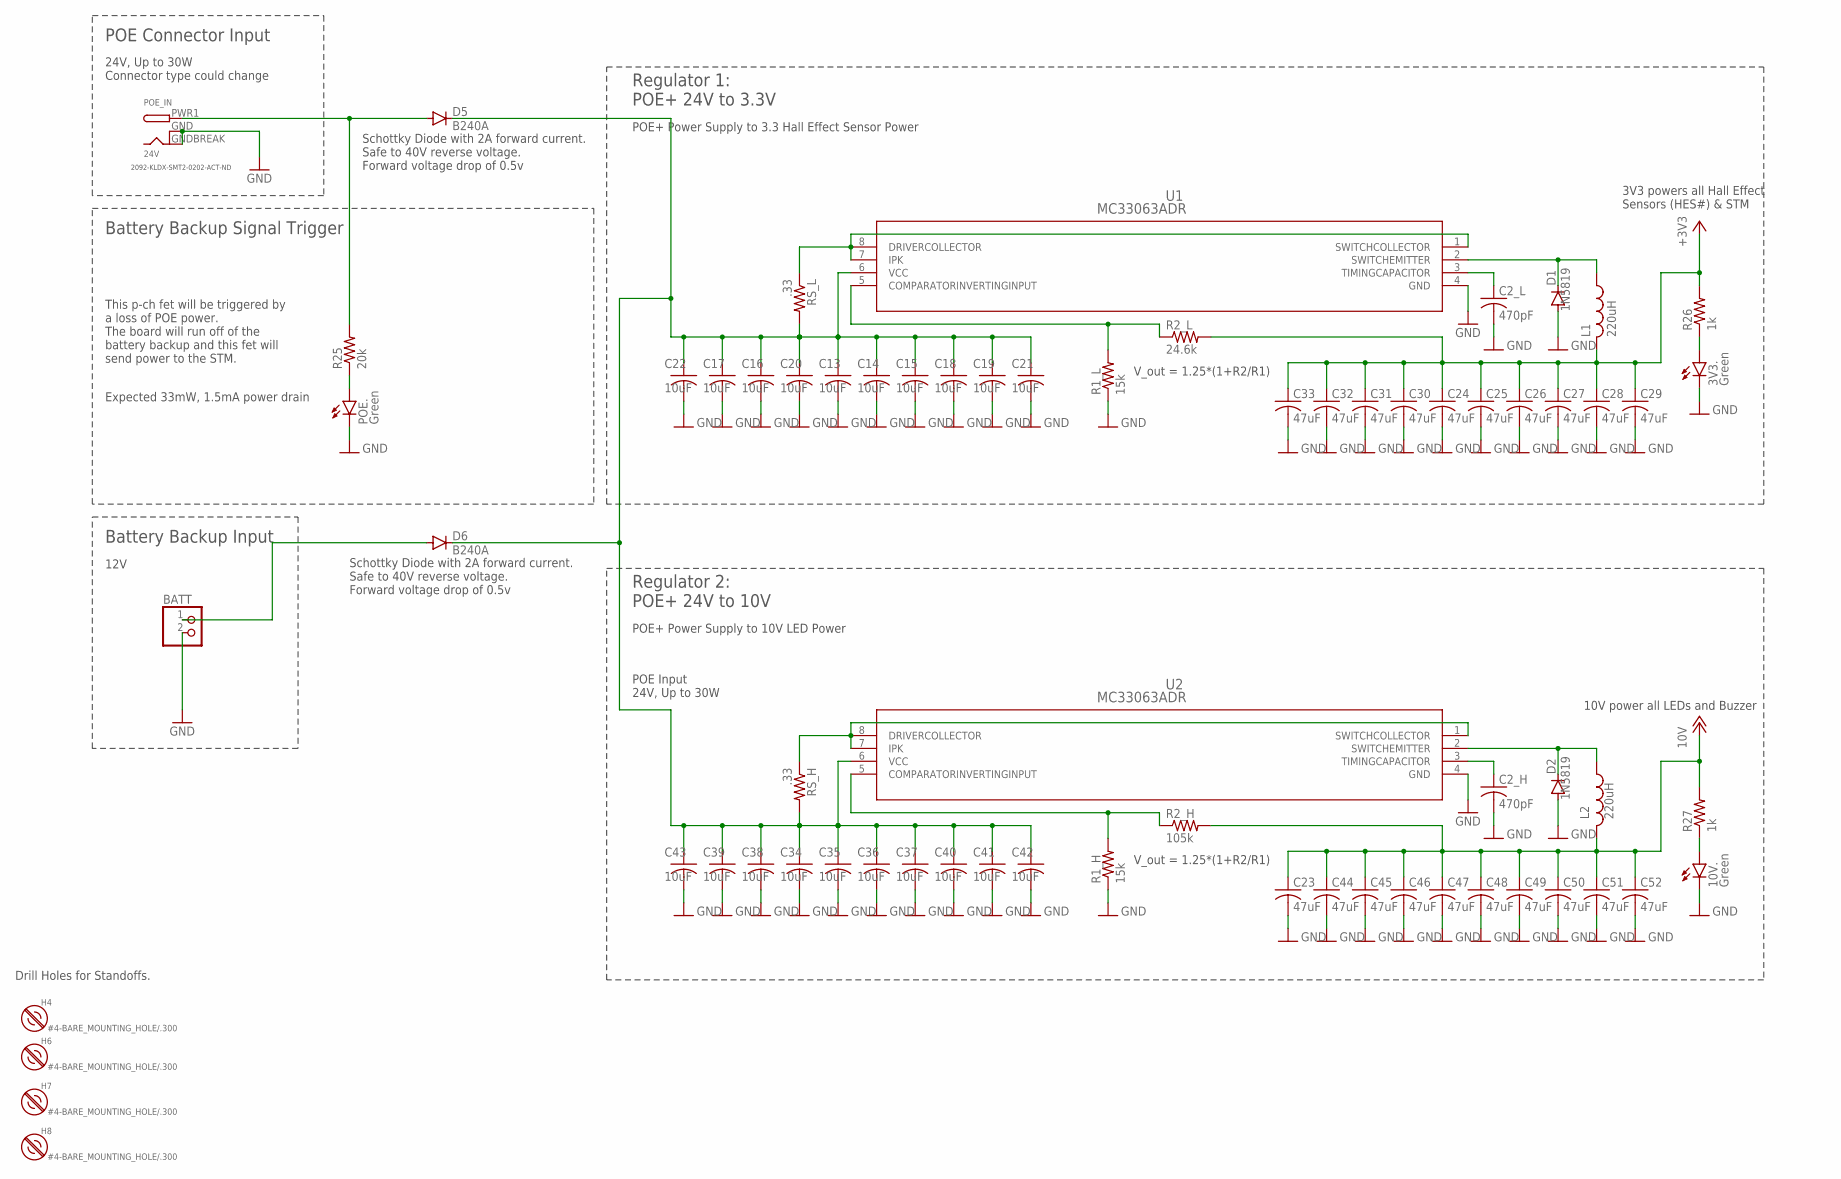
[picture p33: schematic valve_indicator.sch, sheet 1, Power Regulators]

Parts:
3V3., 10V.: Green; CHIP-LED0603; MPN 5988070107F
BATT: LED1; 1X02; MPN 0022232021
C2_H, C2_L: 470pF; C0603K; MPN 0603B471K500CT
C13, C14, C15, C16, C17, C18, C19, C20, C21, C22: 10uF; C1206K; MPN CL31A106KBHNNNE
C23, C44, C45, C46, C47, C48, C49, C50, C51, C52: 47uF; C1206K; MPN C3216X5R1E476M160AC
C24, C25, C26, C27, C28, C29, C30, C31, C32, C33: 47uF; C0805K; MPN C2012X5R1A476M125AC
C34, C35, C36, C37, C38, C39, C40, C41, C42, C43: 10uF; C0805K; MPN GRM21BR61H106ME43L
D1, D2: 1N5819; SOD123; MPN 1N5819HW-7-F
D5, D6: B240A; DO214AC; MPN B240A-13-F
H4, H6, H7, H8: #4-BARE_MOUNTING_HOLE/.300; #4/.300-BARE+STD_NUT_OR_STAR_WASHER
L1, L2: 220uH; 0207/7; MPN 12RS224C
POE.: Green; CHIP-LED0603; MPN 5988070107F
POE_IN: 24V; DCJACK_2MM_SMT; MPN KLDX-SMT2-0202-ATR
R1_H, R1_L: 15k; .0805-C-NOSILK; MPN CRCW080515K0FKEAHP
R2_H: 105k; R1210; MPN ERJ-14NF1053U
R2_L: 24.6k; .0805-C-NOSILK; MPN CRCW080524K9FKEAHP
R25: 20k; .0603-C-NOSILK; MPN ESR03EZPJ203
R26, R27: 1k; .0603-C-NOSILK; MPN SDR03EZPJ102
RS_H: .33; .0603-C-NOSILK; MPN ERJ-3RQFR33V
RS_L: .33; .0603-C-NOSILK; MPN ERJ-3RQFR33V
U1, U2: MC33063ADR; D8; MPN MC33063ADR

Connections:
+3V3: C24.1, C25.1, C26.1, C27.1, C28.1, C29.1, C30.1, C31.1, C32.1, C33.1, L1.3 (2), R2_L.2, R26.2; also elsewhere on the board
+10V: C23.1, C44.1, C45.1, C46.1, C47.1, C48.1, C49.1, C50.1, C51.1, C52.1, L2.3 (2), R2_H.2, R27.2; also elsewhere on the board
GND: 3V3..C, 10V..C, BATT.2, C2_H.2, C2_L.2, C13.2, C14.2, C15.2, C16.2, C17.2, C18.2, C19.2, C20.2, C21.2, C22.2, C23.2, C24.2, C25.2, C26.2, C27.2, C28.2, C29.2, C30.2, C31.2, C32.2, C33.2, C34.2, C35.2, C36.2, C37.2, C38.2, C39.2, C40.2, C41.2, C42.2, C43.2, C44.2, C45.2, C46.2, C47.2, C48.2, C49.2, C50.2, C51.2, C52.2, D1.A, D2.A, POE..C, POE_IN.GND (GNDBREAK), POE_IN.GNDBREAK (GND), R1_H.1, R1_L.1, U1.4 (GND), U2.4 (GND); also elsewhere on the board
unnamed: RS_L.1, U1.1 (SWITCHCOLLECTOR), U1.7 (IPK), U1.8 (DRIVERCOLLECTOR)
unnamed: D1.C, L1.1, U1.2 (SWITCHEMITTER)
unnamed: C2_L.1, U1.3 (TIMINGCAPACITOR)
unnamed: R1_L.2, R2_L.1, U1.5 (COMPARATORINVERTINGINPUT)
unnamed: RS_H.1, U2.1 (SWITCHCOLLECTOR), U2.7 (IPK), U2.8 (DRIVERCOLLECTOR)
unnamed: D5.A, POE_IN.PWR1 (PWR), R25.2
unnamed: POE..A, R25.1
unnamed: D2.C, L2.1, U2.2 (SWITCHEMITTER)
unnamed: BATT.1, D6.A
unnamed: 3V3..A, R26.1
unnamed: C2_H.1, U2.3 (TIMINGCAPACITOR)
unnamed: R1_H.2, R2_H.1, U2.5 (COMPARATORINVERTINGINPUT)
unnamed: 10V..A, R27.1
POE: C13.1, C14.1, C15.1, C16.1, C17.1, C18.1, C19.1, C20.1, C21.1, C22.1, C34.1, C35.1, C36.1, C37.1, C38.1, C39.1, C40.1, C41.1, C42.1, C43.1, D5.C, D6.C, RS_H.2, RS_L.2, U1.6 (VCC), U2.6 (VCC)

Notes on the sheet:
POE Connector Input
Regulator 1: POE+ 24V to 3.3V
3V3 powers all Hall Effect Sensors (HES#) & STM
POE+ Power Supply to 3.3 Hall Effect Sensor Power
POE Input 24V, Up to 30W
Regulator 2: POE+ 24V to 10V
10V power all LEDs and Buzzer
POE+ Power Supply to 10V LED Power
Battery Backup Input
Schottky Diode with 2A forward current. Safe to 40V reverse voltage. Forward voltage drop of 0.5v
This p-ch fet will be triggered by a loss of POE power. The board will run off of the battery backup and this fet will send power to the STM.
V_out = 1.25*(1+R2/R1)
Expected 33mW, 1.5mA power drain
12V
24V, Up to 30W Connector type could change
Battery Backup Signal Trigger
2092-KLDX-SMT2-0202-ACT-ND
Drill Holes for Standoffs.

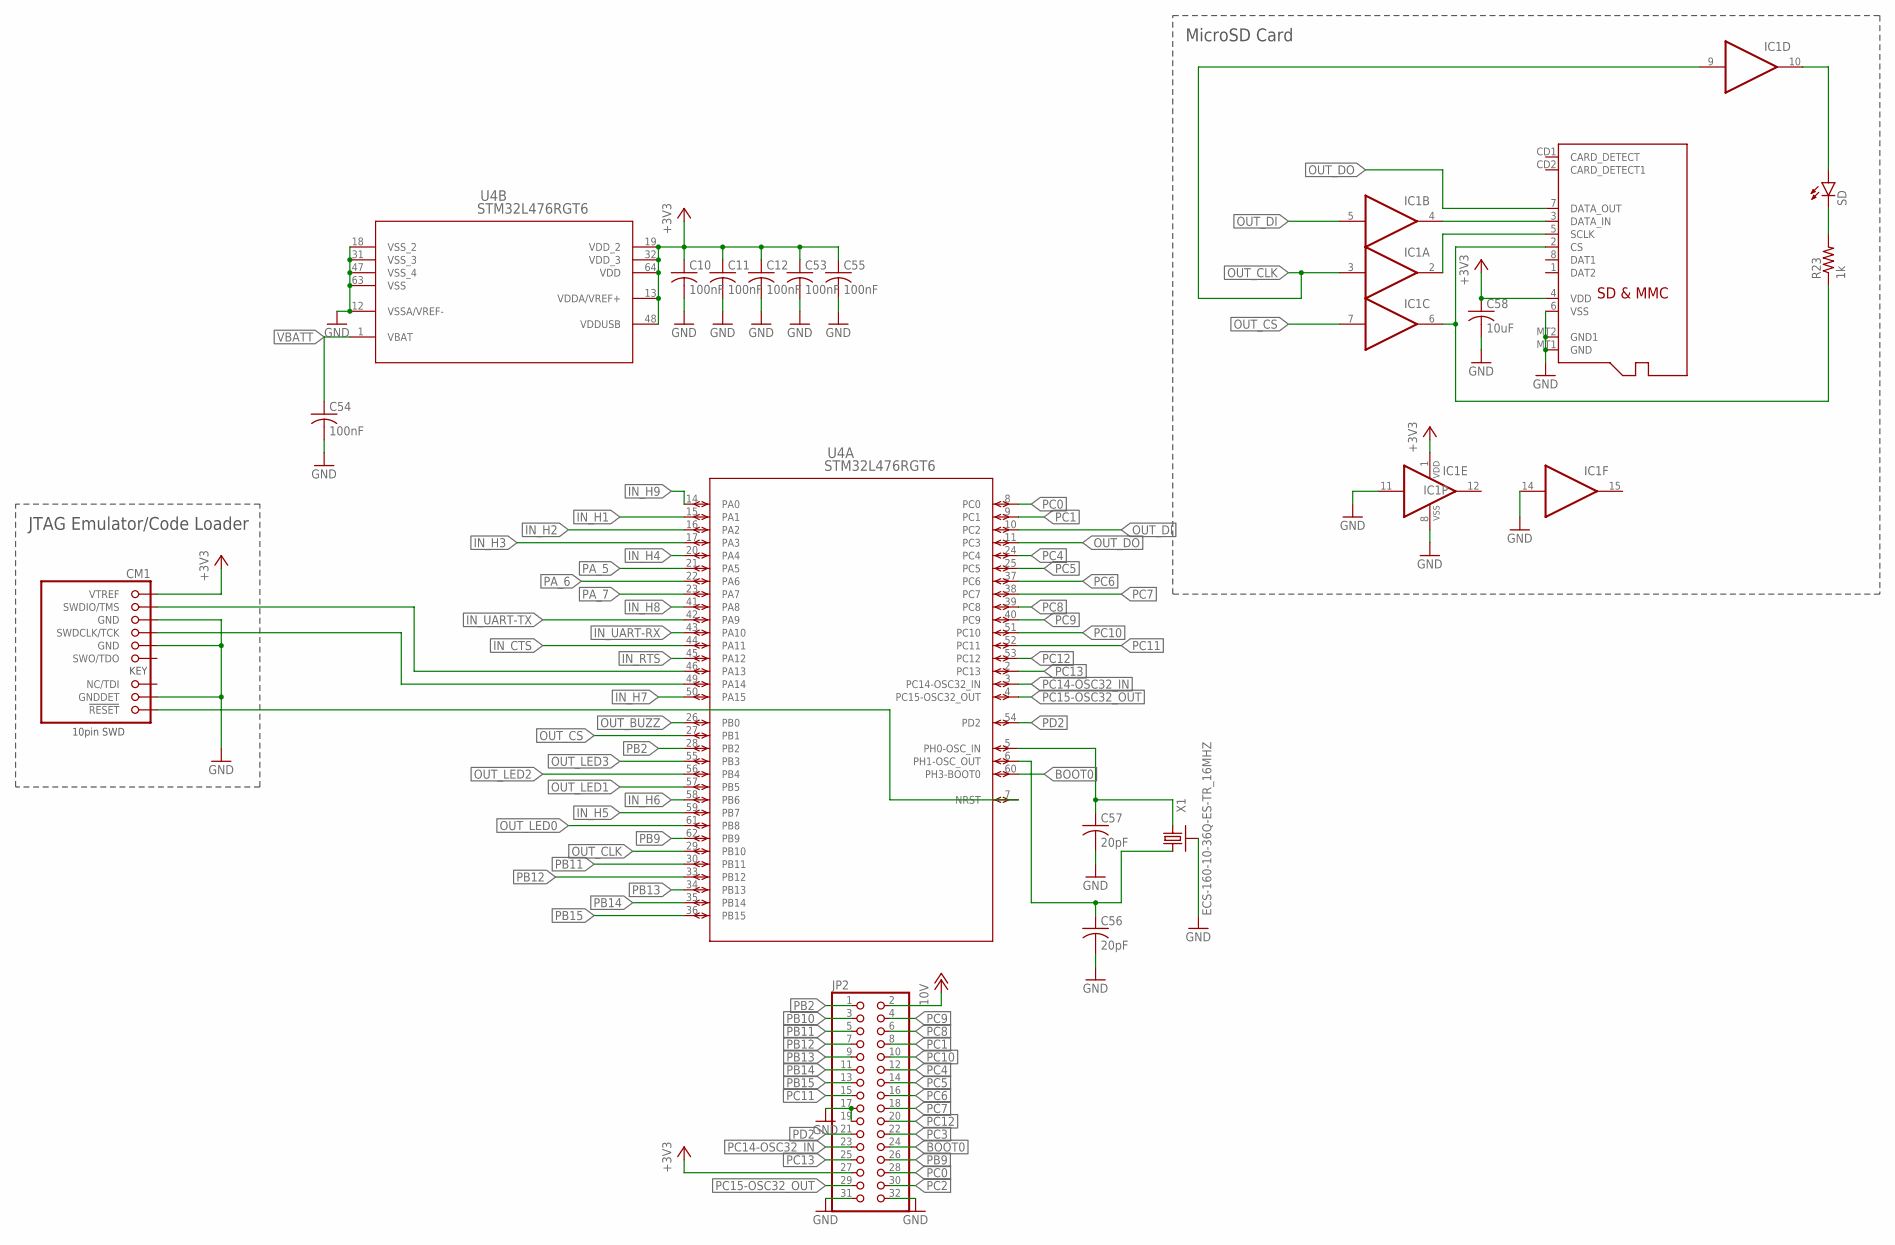
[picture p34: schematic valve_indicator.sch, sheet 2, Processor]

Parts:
C10, C11, C12, C53, C54, C55: 100nF; C0603K; MPN CL10B104KA8NNNC
C56, C57: 20pF; C0402K; MPN CBR04C200F5GAC
C58: 10uF; C0805K; MPN CL21A106KPFNNNG
CM1: FTSH-105-XX-X-DV-K; CON10_2X5_DUK_FTSH; MPN FTSH-105-01-F-DV-K-TR
IC1: 4050D; SO16; MPN CD74HC4050M
JP2: PINHD-2X16; 2X16; MPN PRPC016DAAN-RC
R23: 1k; .0603-C-NOSILK; MPN SDR03EZPJ102
SD: LEDCHIP-LED0603; CHIP-LED0603; MPN 5988070107F
U4: STM32L476RGT6; LQFP64-10X10MM_STM; MPN STM32L476RGT6
X1: ECS-160-10-36Q-ES-TR_16MHZ; 2.5X2.0; MPN ECS-160-10-36Q-ES-TR
X2: MICROSD; MPN MEM2061-01-188-00-A

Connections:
+3V3: C10.1, C11.1, C12.1, C53.1, C55.1, C58.1, CM1.1 (VTREF), IC1.1 (VDD), JP2.27, U4.13 (VDDA/VREF+), U4.19 (VDD_2), U4.32 (VDD_3), U4.48 (VDDUSB), U4.64 (VDD), X2.4 (VDD); also elsewhere on the board
+10V: JP2.2; also elsewhere on the board
BOOT0: JP2.24, U4.60 (PH3-BOOT0)
GND: C10.2, C11.2, C12.2, C53.2, C54.2, C55.2, C56.2, C57.2, C58.2, CM1.3 (GND), CM1.5 (GND), CM1.9 (GNDDET), IC1.8 (VSS), IC1.11 (I), IC1.14 (I), JP2.17, JP2.19, JP2.31, JP2.32, U4.12 (VSSA/VREF-), U4.18 (VSS_2), U4.31 (VSS_3), U4.47 (VSS_4), U4.63 (VSS), X1.2 (SHIELD), X1.4 (SHIELD), X2.6 (VSS), X2.MT1 (GND), X2.MT2 (GND1); also elsewhere on the board
IN_CTS: U4.44 (PA11); also elsewhere on the board
IN_H1: U4.15 (PA1); also elsewhere on the board
IN_H2: U4.16 (PA2); also elsewhere on the board
IN_H3: U4.17 (PA3); also elsewhere on the board
IN_H4: U4.20 (PA4); also elsewhere on the board
IN_H5: U4.59 (PB7); also elsewhere on the board
IN_H6: U4.58 (PB6); also elsewhere on the board
IN_H7: U4.50 (PA15); also elsewhere on the board
IN_H8: U4.41 (PA8); also elsewhere on the board
IN_H9: U4.14 (PA0); also elsewhere on the board
IN_RTS: U4.45 (PA12); also elsewhere on the board
IN_UART-RX: U4.43 (PA10); also elsewhere on the board
IN_UART-TX: U4.42 (PA9); also elsewhere on the board
unnamed: IC1.10 (O), SD.A
unnamed: IC1.2 (O), X2.5 (SCLK)
unnamed: CM1.4 (SWDCLK/TCK), U4.49 (PA14)
unnamed: IC1.6 (O), R23.1, X2.2 (CS)
unnamed: R23.2, SD.C
unnamed: IC1.4 (O), X2.3 (DATA_IN)
unnamed: CM1.2 (SWDIO/TMS), U4.46 (PA13)
unnamed: CM1.10 (!RESET), U4.7 (NRST)
OSC_IN: C57.1, U4.5 (PH0-OSC_IN), X1.3 (2)
OSC_OUT: C56.1, U4.6 (PH1-OSC_OUT), X1.1
OUT_BUZZ: U4.26 (PB0); also elsewhere on the board
OUT_CLK: IC1.3 (I), IC1.9 (I), U4.29 (PB10)
OUT_CS: IC1.7 (I), U4.27 (PB1)
OUT_DI: IC1.5 (I), U4.10 (PC2)
OUT_DO: U4.11 (PC3), X2.7 (DATA_OUT)
OUT_LED0: U4.61 (PB8); also elsewhere on the board
OUT_LED1: U4.57 (PB5); also elsewhere on the board
OUT_LED2: U4.56 (PB4); also elsewhere on the board
OUT_LED3: U4.55 (PB3); also elsewhere on the board
PA_5: U4.21 (PA5)
PA_6: U4.22 (PA6)
PA_7: U4.23 (PA7)
PB2: JP2.1, U4.28 (PB2)
PB9: JP2.26, U4.62 (PB9)
PB10: JP2.3
PB11: JP2.5, U4.30 (PB11)
PB12: JP2.7, U4.33 (PB12)
PB13: JP2.9, U4.34 (PB13)
PB14: JP2.11, U4.35 (PB14)
PB15: JP2.13, U4.36 (PB15)
PC0: JP2.28, U4.8 (PC0)
PC1: JP2.8, U4.9 (PC1)
PC2: JP2.30
PC3: JP2.22
PC4: JP2.12, U4.24 (PC4)
PC5: JP2.14, U4.25 (PC5)
PC6: JP2.16, U4.37 (PC6)
PC7: JP2.18, U4.38 (PC7)
PC8: JP2.6, U4.39 (PC8)
PC9: JP2.4, U4.40 (PC9)
PC10: JP2.10, U4.51 (PC10)
PC11: JP2.15, U4.52 (PC11)
PC12: JP2.20, U4.53 (PC12)
PC13: JP2.25, U4.2 (PC13)
PC14-OSC32_IN: JP2.23, U4.3 (PC14-OSC32_IN)
PC15-OSC32_OUT: JP2.29, U4.4 (PC15-OSC32_OUT)
PD2: JP2.21, U4.54 (PD2)
VBATT: C54.1, U4.1 (VBAT)

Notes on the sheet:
JTAG Emulator/Code Loader
MicroSD Card

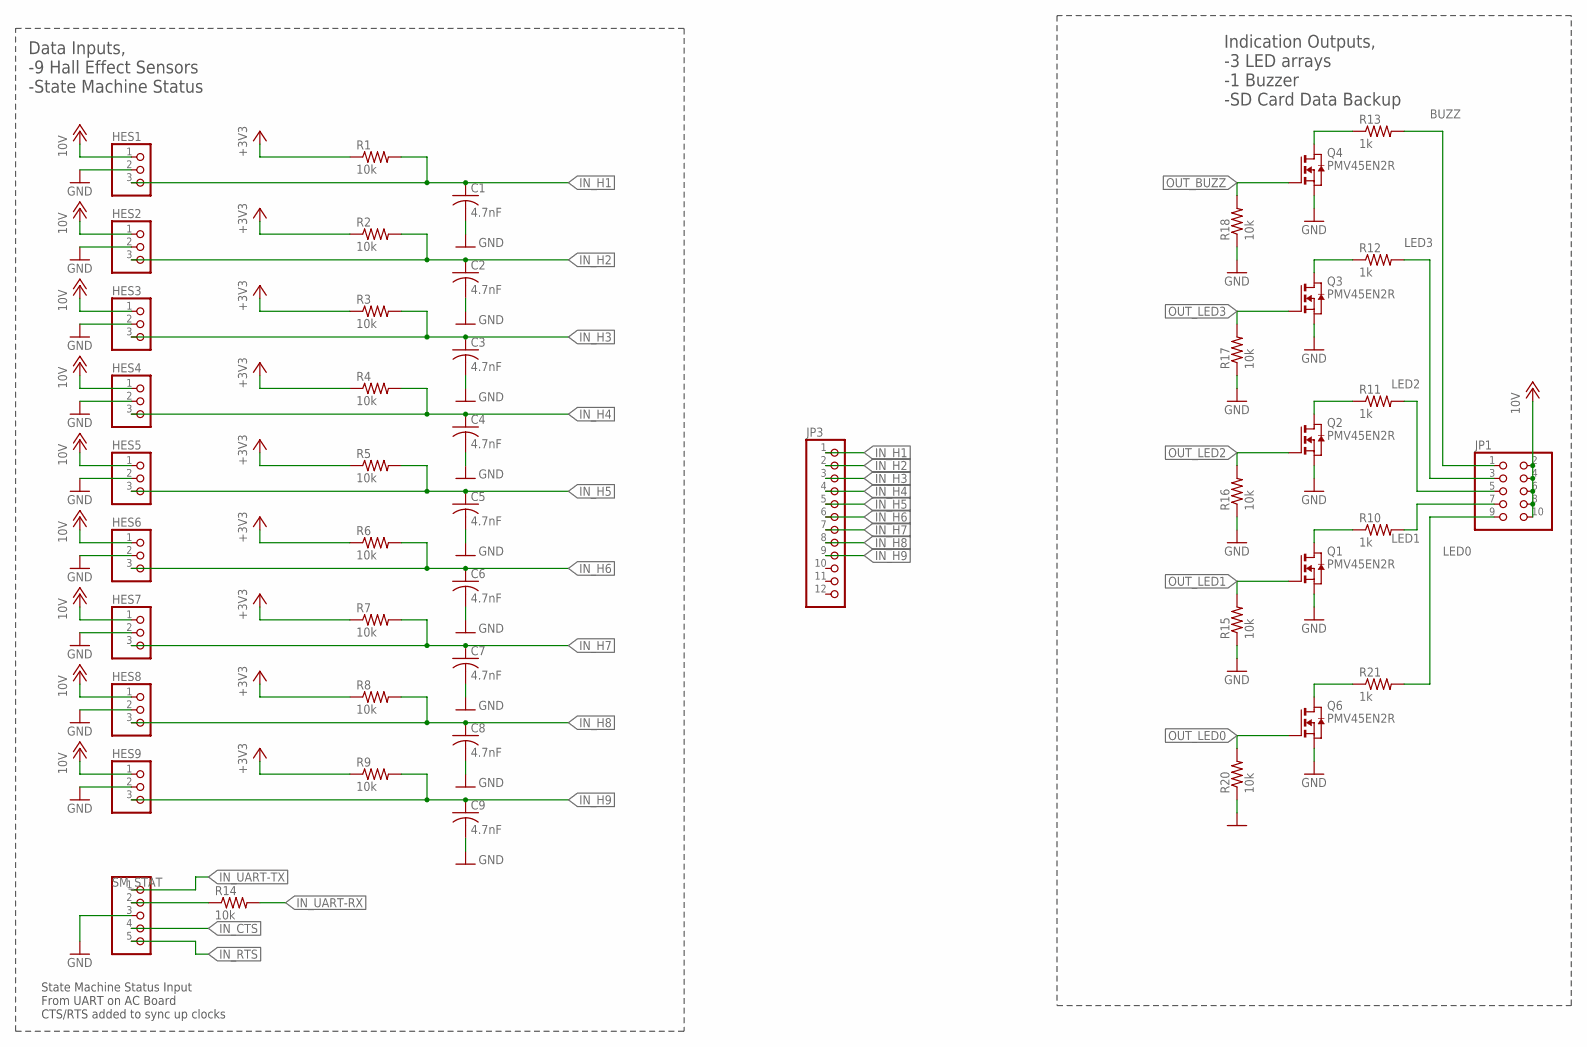
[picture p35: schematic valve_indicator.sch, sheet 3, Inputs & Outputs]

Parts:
C1: 4.7nF; C0603; MPN C1608C0G1H472J080AA
C2, C3, C4, C5, C6, C7, C8, C9: 4.7nF; C0603K; MPN C1608C0G1H472J080AA
HES1: HES1; 1X03; MPN 1718570003
HES2: HES2; 1X03; MPN 1718570003
HES3: HES3; 1X03; MPN 1718570003
HES4: HES4; 1X03; MPN 1718570003
HES5: HES5; 1X03; MPN 1718570003
HES6: HES6; 1X03; MPN 1718570003
HES7: HES7; 1X03; MPN 1718570003
HES8: HES8; 1X03; MPN 1718570003
HES9: HES9; 1X03; MPN 1718570003
JP1: PINHD-2X5; 2X05; MPN AWHW 10A-0202-T
JP3: PINHD-1X12; 1X12; MPN 1718570012
Q1, Q2, Q3, Q4, Q6: PMV45EN2R; SOT23; MPN PMV45EN2R
R1, R2, R3, R4, R5, R6, R7, R8, R9, R14, R15, R16, R17, R18, R20: 10k; .0603-C-NOSILK; MPN RMCF0603FT10K0
R10, R11, R12, R13: 1k; .0603-C-NOSILK; MPN RMCF0603JJ1K00
R21: 1k; R0603; MPN RMCF0603JJ1K00
SM_STAT: SM_STAT; 1X05; MPN AWHW 10A-0202-T

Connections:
+3V3: R1.1, R2.1, R3.1, R4.1, R5.1, R6.1, R7.1, R8.1, R9.1; also elsewhere on the board
+10V: HES1.1, HES2.1, HES3.1, HES4.1, HES5.1, HES6.1, HES7.1, HES8.1, HES9.1, JP1.2, JP1.4, JP1.6, JP1.8, JP1.10; also elsewhere on the board
BUZZ: JP1.1, R13.2
GND: C1.2, C2.2, C3.2, C4.2, C5.2, C6.2, C7.2, C8.2, C9.2, HES1.2, HES2.2, HES3.2, HES4.2, HES5.2, HES6.2, HES7.2, HES8.2, HES9.2, Q1.2 (S), Q2.2 (S), Q3.2 (S), Q4.2 (S), Q6.2 (S), R15.1, R16.1, R17.1, R18.1, R20.1, SM_STAT.3; also elsewhere on the board
IN_CTS: SM_STAT.4; also elsewhere on the board
IN_H1: C1.1, HES1.3, JP3.1, R1.2; also elsewhere on the board
IN_H2: C2.1, HES2.3, JP3.2, R2.2; also elsewhere on the board
IN_H3: C3.1, HES3.3, JP3.3, R3.2; also elsewhere on the board
IN_H4: C4.1, HES4.3, JP3.4, R4.2; also elsewhere on the board
IN_H5: C5.1, HES5.3, JP3.5, R5.2; also elsewhere on the board
IN_H6: C6.1, HES6.3, JP3.6, R6.2; also elsewhere on the board
IN_H7: C7.1, HES7.3, JP3.7, R7.2; also elsewhere on the board
IN_H8: C8.1, HES8.3, JP3.8, R8.2; also elsewhere on the board
IN_H9: C9.1, HES9.3, JP3.9, R9.2; also elsewhere on the board
IN_RTS: SM_STAT.5; also elsewhere on the board
IN_UART-RX: R14.2; also elsewhere on the board
IN_UART-TX: SM_STAT.1; also elsewhere on the board
LED0: JP1.9, R21.2
LED1: JP1.7, R10.2
LED2: JP1.5, R11.2
LED3: JP1.3, R12.2
unnamed: Q4.3 (D), R13.1
unnamed: Q6.3 (D), R21.1
unnamed: Q3.3 (D), R12.1
unnamed: Q1.3 (D), R10.1
unnamed: Q2.3 (D), R11.1
OUT_BUZZ: Q4.1 (G), R18.2; also elsewhere on the board
OUT_LED0: Q6.1 (G), R20.2; also elsewhere on the board
OUT_LED1: Q1.1 (G), R15.2; also elsewhere on the board
OUT_LED2: Q2.1 (G), R16.2; also elsewhere on the board
OUT_LED3: Q3.1 (G), R17.2; also elsewhere on the board
UART_RX: R14.1, SM_STAT.2

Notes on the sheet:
State Machine Status Input From UART on AC Board CTS/RTS added to sync up clocks
Data Inputs, -9 Hall Effect Sensors -State Machine Status
Indication Outputs, -3 LED arrays -1 Buzzer -SD Card Data Backup

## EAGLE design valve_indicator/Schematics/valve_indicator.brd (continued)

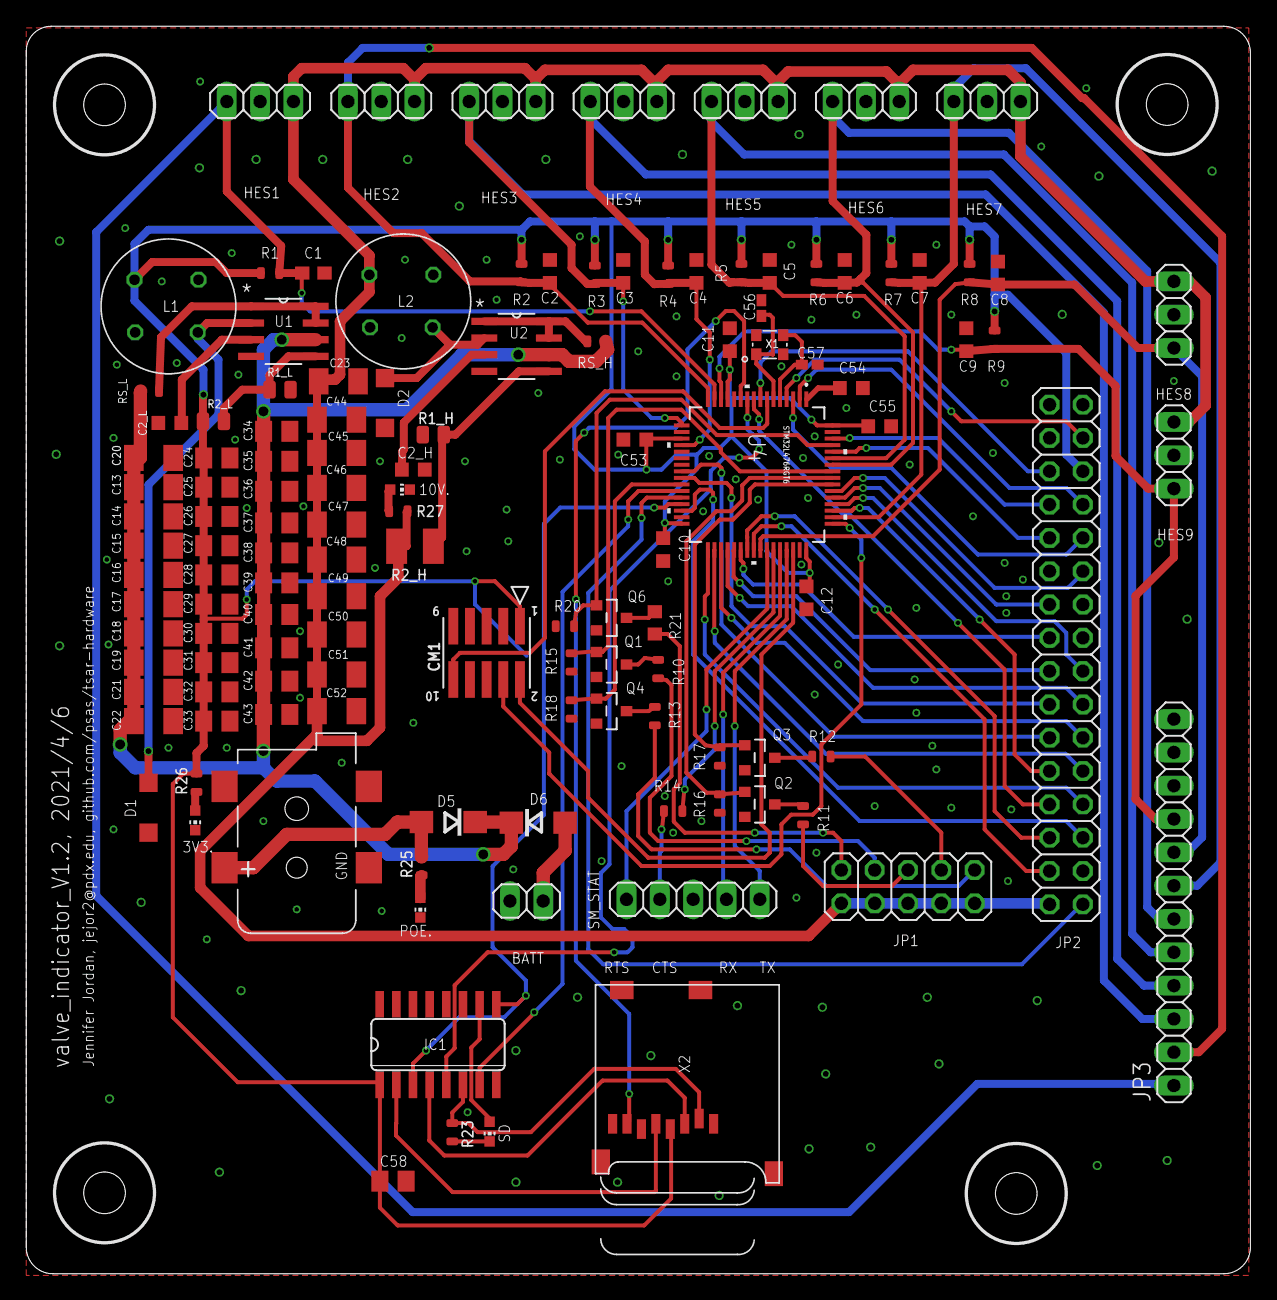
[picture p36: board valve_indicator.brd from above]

Board: 2 copper layers, 93.3 x 95.1 mm, 131 parts (0 on the bottom side), 84 nets.

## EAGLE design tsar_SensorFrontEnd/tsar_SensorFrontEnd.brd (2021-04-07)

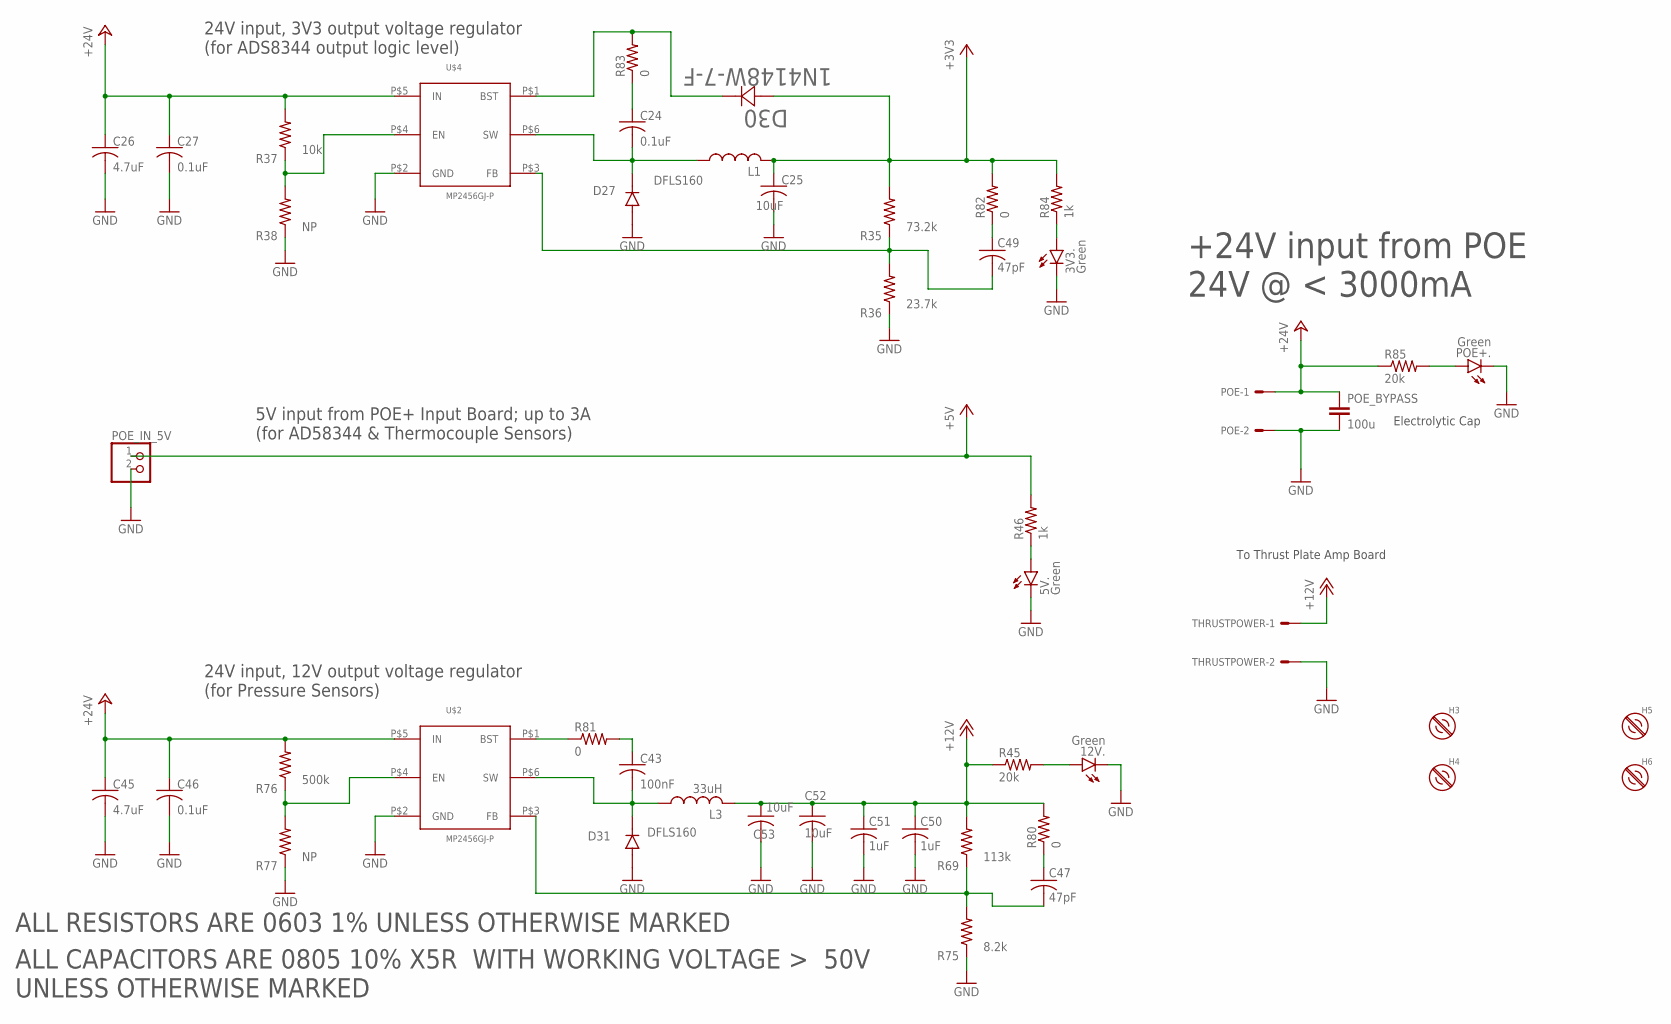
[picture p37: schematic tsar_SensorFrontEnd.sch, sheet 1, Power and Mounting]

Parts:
3V3., 5V., 12V.: Green; CHIP-LED0603; MPN 5988070107F
C24, C27, C46: 0.1uF; C0603K; MPN CL10B104KB8NNNL
C25, C52, C53: 10uF; C1206K; MPN CL31A106MBHNNNE
C26, C45: 4.7uF; C0805K; MPN CL21A475KBQNNNE
C43: 100nF; C0603K; MPN CL10B104KB8NNNL
C47, C49: 47pF; C0603K; MPN C1608C0G1H470J080AA
C50, C51: 1uF; C0603K; MPN CL10A105KB8NNNC
D27, D31: DFLS160; POWERDI-123; MPN DFLS160-7
D30: 1N4148W-7-F; SOD123; MPN 1N4148W-7-F
H3, H4, H5, H6: #4-BARE_MOUNTING_HOLE/.300; #4/.300-BARE+STD_NUT_OR_STAR_WASHER
L1: CLF5030NIT-100M-D; 0.209"LX0.197"W(5.30MMX5.00MM); MPN CLF5030NIT-100M-D
L3: 33uH; 0.209"LX0.197"W(5.30MMX5.00MM); MPN PM4340.333NLT
POE: 22-23-2021
POE+.: Green; CHIP-LED0603; MPN 5988070107F
POE_BYPASS: 100u; C2.5-4; MPN ECA-1HM101
POE_IN_5V: PINHD-1X2; 1X02; MPN 0022232021
R35: 73.2k; .0805-A-NOSILK; MPN RK73H2ATTD7322F
R36: 23.7k; .0805-A-NOSILK; MPN RK73H2ATTD2372F
R37: 10k; .0805-B; MPN ESR03EZPF1002
R38: NP; R0603
R45, R85: 20k; .0603-A-NOSILK; MPN ERJ-PA3J203V
R46, R84: 1k; .0603-A-NOSILK; MPN ERJ-PA3F1001V
R69: 113k; .0805-A-NOSILK; MPN RK73H2ATTD1133F
R75: 8.2k; .0805-A-NOSILK; MPN RK73H2ATTD8201F
R76: 500k; 1206-A; MPN CRMA1206AF500KFKEF
R77: NP; .0805-A-NOSILK
R80, R81, R82, R83: 0; .0603-A-NOSILK; MPN RCS06030000Z0EA
THRUSTPOWER: 22-23-2021
U$2, U$4: MP2456GJ-P; SOT6; MPN MP2456GJ-P

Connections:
+3V3: C25.1, D30.2, L1.2, R35.2, R82.2, R84.2; also elsewhere on the board
+5V: POE_IN_5V.1, R46.2; also elsewhere on the board
+12V: C50.1, C51.1, C52.1, C53.1, L3.2, R45.1, R69.2, R80.2, THRUSTPOWER.1; also elsewhere on the board
+24V: C26.1, C27.1, C45.1, C46.1, POE.1, POE_BYPASS.1, R37.2, R76.2, R85.1, U$2.P$5 (IN), U$4.P$5 (IN)
FLY1: C24.2, D27.C, L1.1, U$4.P$6 (SW)
FLY3: C43.2, D31.C, L3.1, U$2.P$6 (SW)
GND: 3V3..C, 5V..C, 12V..C, C25.2, C26.2, C27.2, C45.2, C46.2, C50.2, C51.2, C52.2, C53.2, D27.A, D31.A, POE.2, POE+..C, POE_BYPASS.2, POE_IN_5V.2, R36.1, R38.1, R75.1, R77.1, THRUSTPOWER.2, U$2.P$2 (GND), U$4.P$2 (GND); also elsewhere on the board
unnamed: C24.1, R83.1
unnamed: D30.1, R83.2, U$4.P$1 (BST)
unnamed: R37.1, R38.2, U$4.P$4 (EN)
unnamed: C43.1, R81.2
unnamed: C47.2, R69.1, R75.2, U$2.P$3 (FB)
unnamed: R76.1, R77.2, U$2.P$4 (EN)
unnamed: C47.1, R80.1
unnamed: R81.1, U$2.P$1 (BST)
unnamed: C49.2, R35.1, R36.2, U$4.P$3 (FB)
unnamed: C49.1, R82.1
unnamed: 3V3..A, R84.1
unnamed: 5V..A, R46.1
unnamed: 12V..A, R45.2
unnamed: POE+..A, R85.2

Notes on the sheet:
24V input, 3V3 output voltage regulator (for ADS8344 output logic level)
ALL RESISTORS ARE 0603 1% UNLESS OTHERWISE MARKED
ALL CAPACITORS ARE 0805 10% X5R WITH WORKING VOLTAGE > 50V UNLESS OTHERWISE MARKED
+24V input from POE 24V @ < 3000mA
Electrolytic Cap
24V input, 12V output voltage regulator (for Pressure Sensors)
5V input from POE+ Input Board; up to 3A (for AD58344 & Thermocouple Sensors)
To Thrust Plate Amp Board

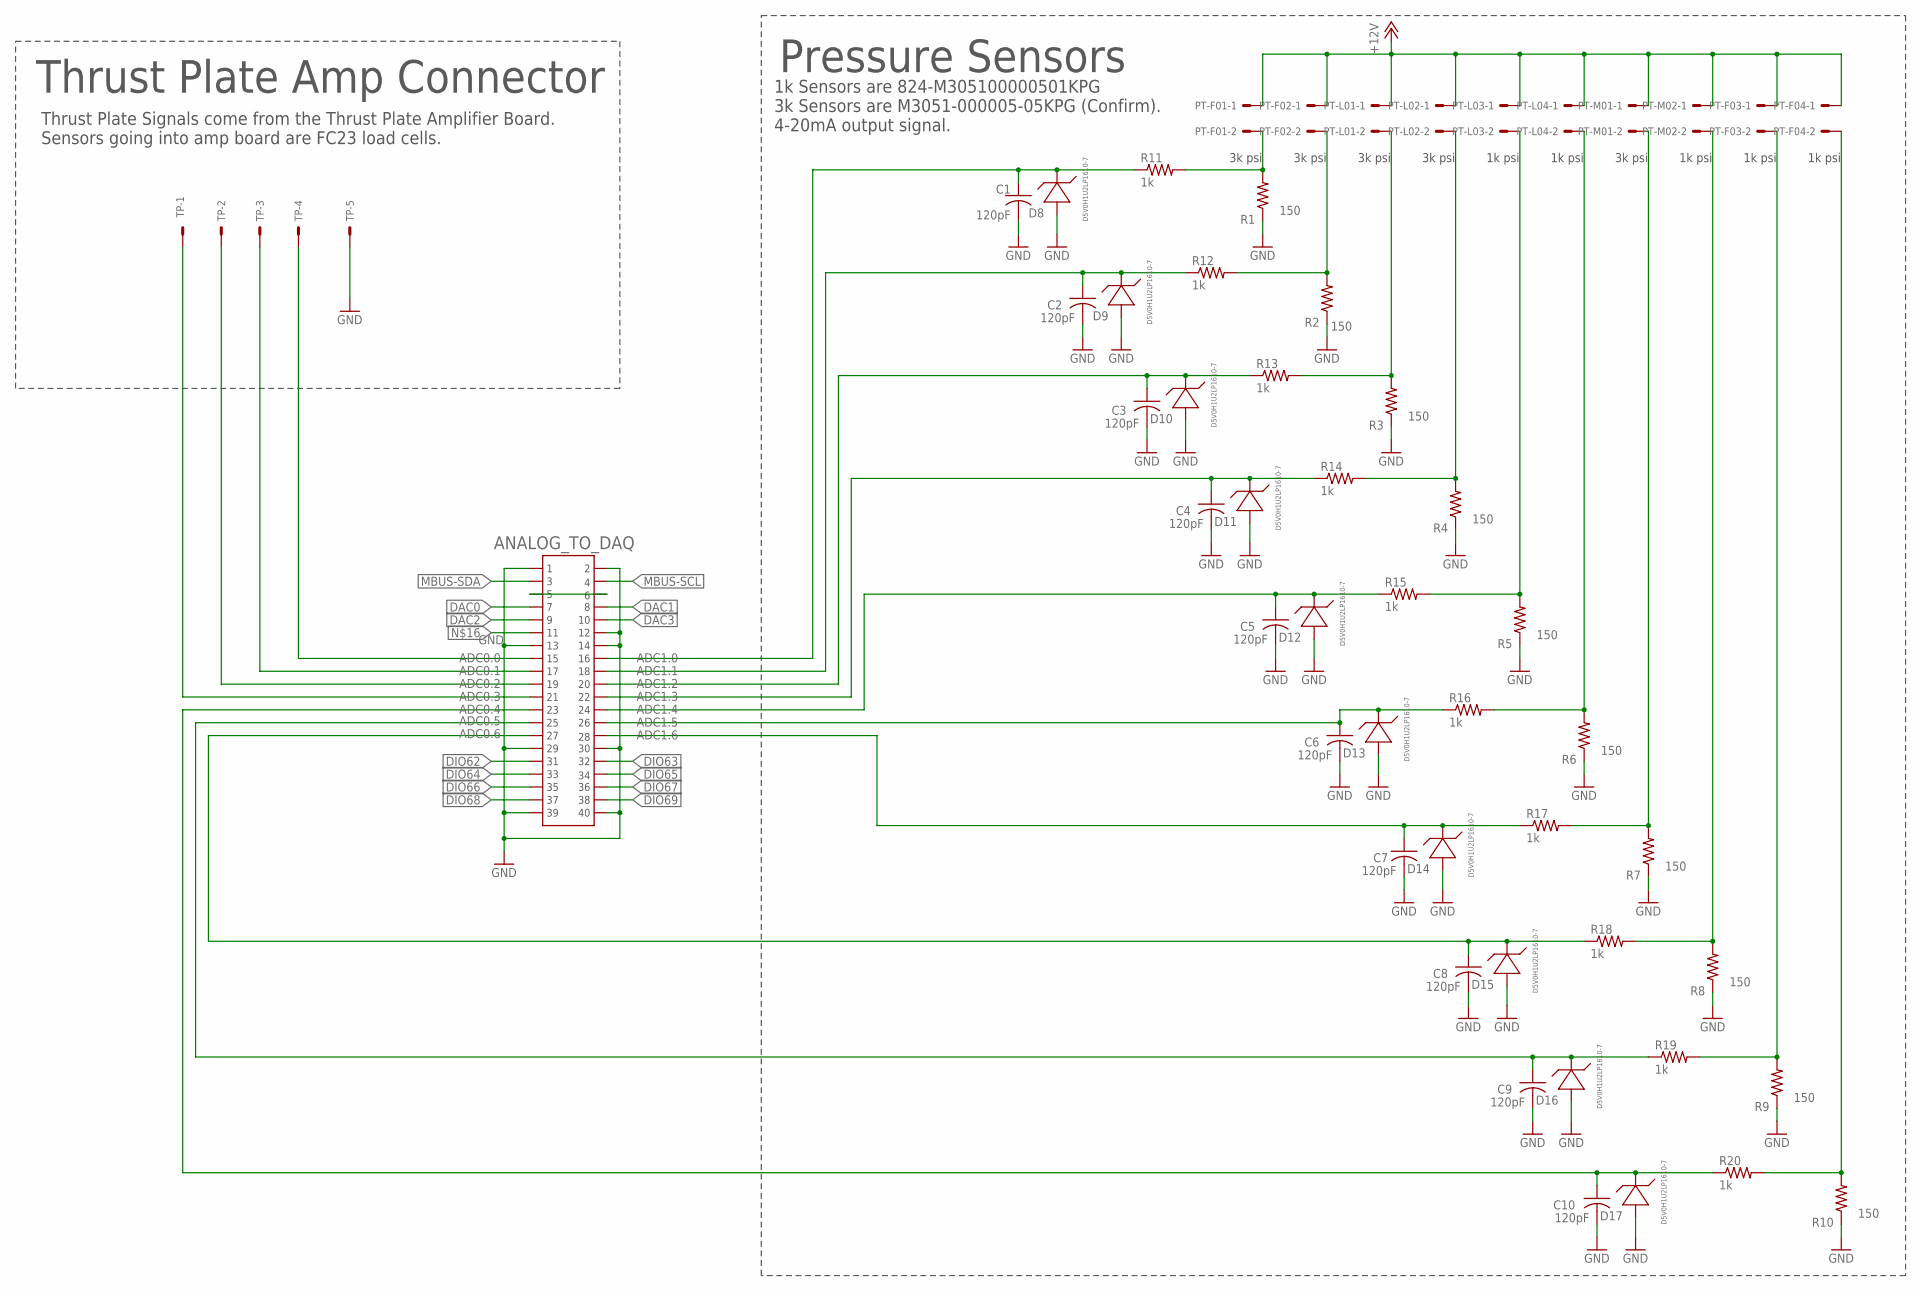
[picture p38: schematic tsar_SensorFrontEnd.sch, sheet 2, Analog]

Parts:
ANALOG_TO_DAQ: IDC_RECEPTACLE_2X20-S9175-ND; IDC_RECEPTACLES; MPN SBH11-PBPC-D20-ST-BK
C1, C2, C3, C4, C5, C6, C7, C8, C9, C10: 120pF; C0603K; MPN CL10C121JB8NNNC
D8, D9, D10, D11, D12, D13, D14, D15, D16, D17: D5V0H1U2LP1610-7; 0603DIODE; MPN D5V0H1U2LP1610-7
PT-F01, PT-F02, PT-F03, PT-F04: 22-23-2021
PT-L01, PT-L02, PT-L03, PT-L04: 22-23-2021
PT-M01, PT-M02: 22-23-2021
R1, R2, R3, R4, R5, R6, R7, R8, R9, R10: 150; .0805-A-NOSILK; MPN 4-2176091-1
R11, R12, R13, R14, R15, R16, R17, R18, R19, R20: 1k; .0603-A-NOSILK; MPN ERJ-PA3F1001V
TP: 22-23-2051

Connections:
+12V: PT-F01.1, PT-F02.1, PT-F03.1, PT-F04.1, PT-L01.1, PT-L02.1, PT-L03.1, PT-L04.1, PT-M01.1, PT-M02.1; also elsewhere on the board
ADC0.0: ANALOG_TO_DAQ.15, TP.4
ADC0.1: ANALOG_TO_DAQ.17, TP.3
ADC0.2: ANALOG_TO_DAQ.19, TP.2
ADC0.3: ANALOG_TO_DAQ.21, TP.1
ADC0.4: ANALOG_TO_DAQ.23, C10.1, D17.P$2, R20.1
ADC0.5: ANALOG_TO_DAQ.25, C9.1, D16.P$2, R19.1
ADC0.6: ANALOG_TO_DAQ.27, C8.1, D15.P$2, R18.1
ADC1.0: ANALOG_TO_DAQ.16, C1.1, D8.P$2, R11.1
ADC1.1: ANALOG_TO_DAQ.18, C2.1, D9.P$2, R12.1
ADC1.2: ANALOG_TO_DAQ.20, C3.1, D10.P$2, R13.1
ADC1.3: ANALOG_TO_DAQ.22, C4.1, D11.P$2, R14.1
ADC1.4: ANALOG_TO_DAQ.24, C5.1, D12.P$2, R15.1
ADC1.5: ANALOG_TO_DAQ.26, C6.1, D13.P$2, R16.1
ADC1.6: ANALOG_TO_DAQ.28, C7.1, D14.P$2, R17.1
DAC0: ANALOG_TO_DAQ.7
DAC1: ANALOG_TO_DAQ.8
DAC2: ANALOG_TO_DAQ.9
DAC3: ANALOG_TO_DAQ.10
DIO62: ANALOG_TO_DAQ.31
DIO63: ANALOG_TO_DAQ.32
DIO64: ANALOG_TO_DAQ.33
DIO65: ANALOG_TO_DAQ.34
DIO66: ANALOG_TO_DAQ.35
DIO67: ANALOG_TO_DAQ.36
DIO68: ANALOG_TO_DAQ.37
DIO69: ANALOG_TO_DAQ.38
GND: ANALOG_TO_DAQ.1, ANALOG_TO_DAQ.2, ANALOG_TO_DAQ.12, ANALOG_TO_DAQ.13, ANALOG_TO_DAQ.14, ANALOG_TO_DAQ.29, ANALOG_TO_DAQ.30, ANALOG_TO_DAQ.39, ANALOG_TO_DAQ.40, C1.2, C2.2, C3.2, C4.2, C5.2, C6.2, C7.2, C8.2, C9.2, C10.2, D8.P$1, D9.P$1, D10.P$1, D11.P$1, D12.P$1, D13.P$1, D14.P$1, D15.P$1, D16.P$1, D17.P$1, R1.1, R2.1, R3.1, R4.1, R5.1, R6.1, R7.1, R8.1, R9.1, R10.1, TP.5; also elsewhere on the board
MBUS-SCL: ANALOG_TO_DAQ.4
MBUS-SDA: ANALOG_TO_DAQ.3
unnamed: PT-L02.2, R4.2, R14.2
unnamed: PT-F02.2, R2.2, R12.2
unnamed: ANALOG_TO_DAQ.5, ANALOG_TO_DAQ.6
unnamed: PT-M02.2, R8.2, R18.2
unnamed: PT-F03.2, R9.2, R19.2
unnamed: PT-F01.2, R1.2, R11.2
unnamed: PT-L01.2, R3.2, R13.2
unnamed: PT-L03.2, R5.2, R15.2
unnamed: PT-L04.2, R6.2, R16.2
unnamed: PT-M01.2, R7.2, R17.2
unnamed: PT-F04.2, R10.2, R20.2

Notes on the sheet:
Pressure Sensors
3k psi
1k psi
Thrust Plate Amp Connector
Thrust Plate Signals come from the Thrust Plate Amplifier Board. Sensors going into amp board are FC23 load cells.
1k Sensors are 824-M305100000501KPG 3k Sensors are M3051-000005-05KPG (Confirm). 4-20mA output signal.

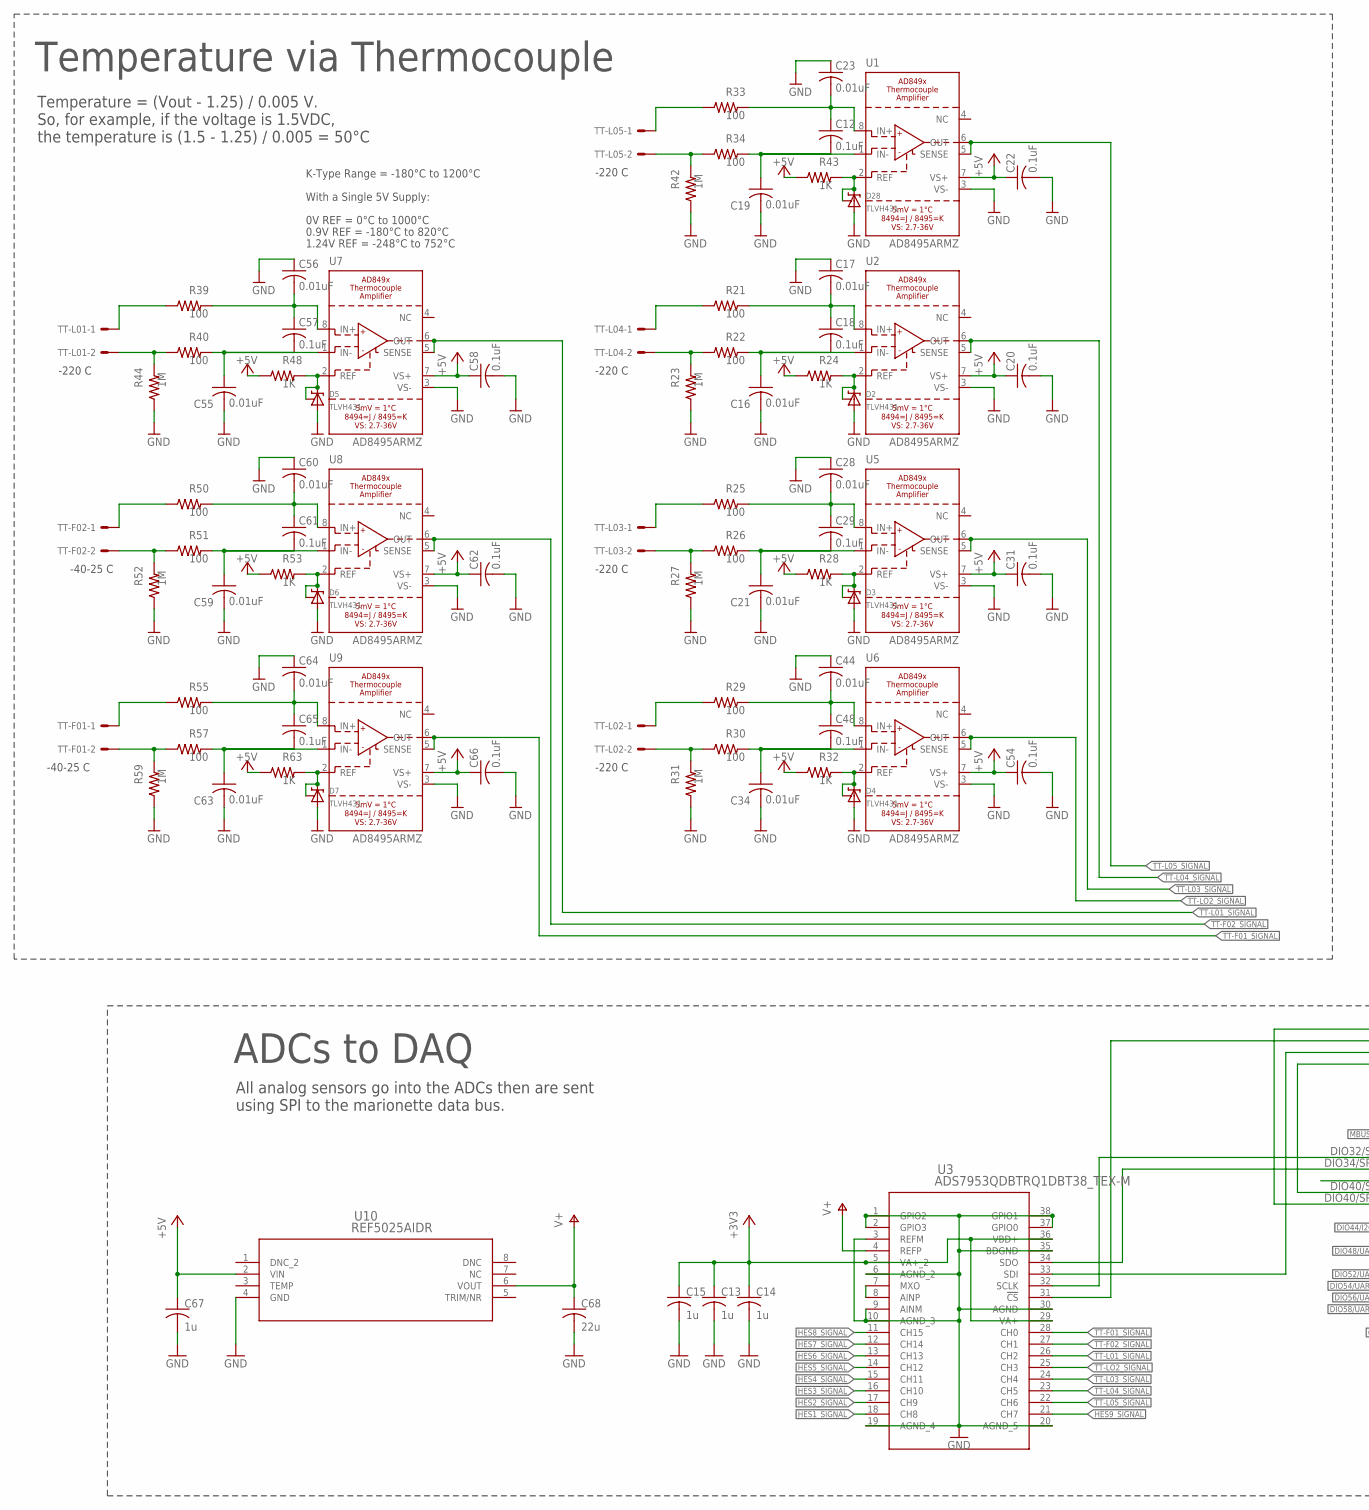
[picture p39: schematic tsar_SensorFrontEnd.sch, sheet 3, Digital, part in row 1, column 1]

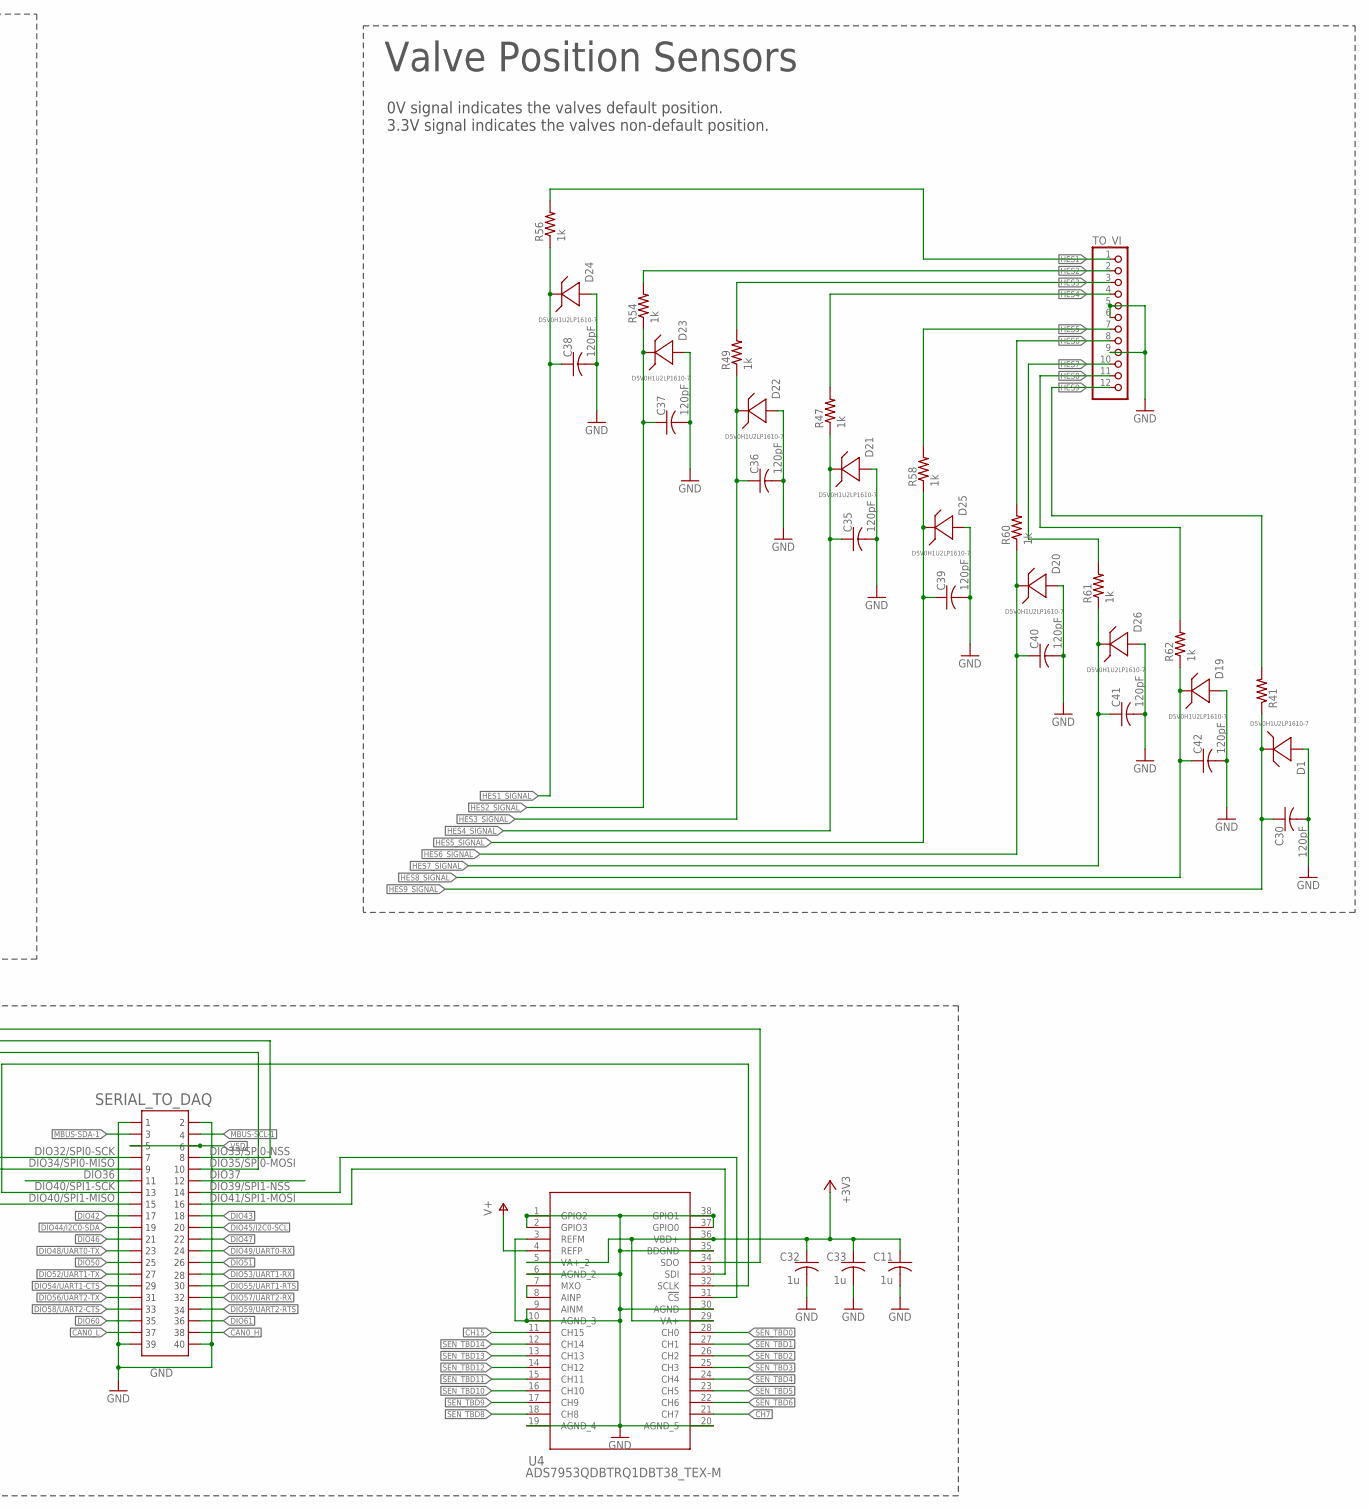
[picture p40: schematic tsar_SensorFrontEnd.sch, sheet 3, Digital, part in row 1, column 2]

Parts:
C11, C13, C14, C15, C32, C33: 1u; C0603K; MPN CL10A105KB8NNNC
C12, C18, C20, C22, C29, C31, C48, C54, C57, C58, C61, C62, C65, C66: 0.1uF; C0603K; MPN CL10B104KB8NNNL
C16, C17, C19, C21, C23, C28, C34, C44, C55, C56, C59, C60, C63, C64: 0.01uF; C0603K; MPN CL10B103KB8NNNC
C30, C35, C36, C37, C38, C39, C40, C41, C42: 120pF; C0603K; MPN CL10C121JB8NNNC
C67: 1u; C0603K; MPN CL10A105KA8NNNC
C68: 22u; C0603K; MPN GRM188C60J226MEA0D
D1, D19, D20, D21, D22, D23, D24, D25, D26: D5V0H1U2LP1610-7; 0603DIODE; MPN D5V0H1U2LP1610-7
D2, D3, D4, D5, D6, D7, D28: TLVH431; SOT23-R; MPN TLVH431AIL3T
R21, R22, R25, R26, R29, R30, R33, R34, R39, R40, R50, R51, R55, R57: 100; .0603-C-NOSILK; MPN SG73P1JTTD1000F
R23, R27, R31, R42, R44, R52, R59: 1M; .0603-C-NOSILK; MPN CMP0603-FX-1004ELF
R24, R28, R32, R43, R48, R53, R63: 1K; .0603-C-NOSILK; MPN SDR03EZPJ102
R41, R47, R49, R54, R56, R58, R60, R61, R62: 1k; .0603-A-NOSILK; MPN ERJ-PA3F1001V
SERIAL_TO_DAQ: IDC_RECEPTACLE_2X20-S9175-ND; IDC_RECEPTACLES; MPN SBH11-PBPC-D20-ST-BK
TO_VI: PINHD-1X12; 1X12; MPN 1718570012
TT-F01, TT-F02: 22-23-2021
TT-L01, TT-L02, TT-L03, TT-L04, TT-L05: 22-23-2021
U1, U2, U5, U6, U7, U8, U9: AD8495ARMZ; MSOP8_0.65MM; MPN AD8495ARMZ
U3, U4: ADS7953QDBTRQ1DBT38_TEX-M; DBT38_TEX-M; MPN ADS7953QDBTRQ1
U10: REF5025AIDR; D8; MPN REF5025AIDR

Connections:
+3V3: C11.1, C13.1, C14.1, C15.1, C32.1, C33.1, U3.5 (VA+_2), U3.29 (VA+), U3.36 (VBD+), U4.5 (VA+_2), U4.29 (VA+), U4.36 (VBD+); also elsewhere on the board
+5V: C20.1, C22.1, C31.1, C54.1, C58.1, C62.1, C66.1, C67.1, R24.1, R28.1, R32.1, R43.1, R48.1, R53.1, R63.1, U1.7 (VS+), U2.7 (VS+), U5.7 (VS+), U6.7 (VS+), U7.7 (VS+), U8.7 (VS+), U9.7 (VS+), U10.2 (VIN); also elsewhere on the board
CAN0_H: SERIAL_TO_DAQ.38
CAN0_L: SERIAL_TO_DAQ.37
CH7: U4.21 (CH7)
CH15: U4.11 (CH15)
DIO32/SPI0-SCK: SERIAL_TO_DAQ.7, U3.32 (SCLK)
DIO33/SPI0-NSS: SERIAL_TO_DAQ.8, U3.31 (!CS)
DIO34/SPI0-MISO: SERIAL_TO_DAQ.9, U3.34 (SDO)
DIO35/SPI0-MOSI: SERIAL_TO_DAQ.10, U3.33 (SDI)
DIO36: SERIAL_TO_DAQ.11
DIO37: SERIAL_TO_DAQ.12
DIO39/SPI1-NSS: SERIAL_TO_DAQ.14, U4.31 (!CS)
DIO40/SPI1-MISO: SERIAL_TO_DAQ.15, U4.34 (SDO)
DIO40/SPI1-SCK: SERIAL_TO_DAQ.13, U4.32 (SCLK)
DIO41/SPI1-MOSI: SERIAL_TO_DAQ.16, U4.33 (SDI)
DIO42: SERIAL_TO_DAQ.17
DIO43: SERIAL_TO_DAQ.18
DIO44/I2C0-SDA: SERIAL_TO_DAQ.19
DIO45/I2C0-SCL: SERIAL_TO_DAQ.20
DIO46: SERIAL_TO_DAQ.21
DIO47: SERIAL_TO_DAQ.22
DIO48/UART0-TX: SERIAL_TO_DAQ.23
DIO49/UART0-RX: SERIAL_TO_DAQ.24
DIO50: SERIAL_TO_DAQ.25
DIO51: SERIAL_TO_DAQ.26
DIO52/UART1-TX: SERIAL_TO_DAQ.27
DIO53/UART1-RX: SERIAL_TO_DAQ.28
DIO54/UART1-CTS: SERIAL_TO_DAQ.29
DIO55/UART1-RTS: SERIAL_TO_DAQ.30
DIO56/UART2-TX: SERIAL_TO_DAQ.31
DIO57/UART2-RX: SERIAL_TO_DAQ.32
DIO58/UART2-CTS: SERIAL_TO_DAQ.33
DIO59/UART2-RTS: SERIAL_TO_DAQ.34
DIO60: SERIAL_TO_DAQ.35
DIO61: SERIAL_TO_DAQ.36
GND: C11.2, C13.2, C14.2, C15.2, C16.2, C17.1, C19.2, C20.2, C21.2, C22.2, C23.1, C28.1, C30.2, C31.2, C32.2, C33.2, C34.2, C35.2, C36.2, C37.2, C38.2, C39.2, C40.2, C41.2, C42.2, C44.1, C54.2, C55.2, C56.1, C58.2, C59.2, C60.1, C62.2, C63.2, C64.1, C66.2, C67.2, C68.2, D1.P$1, D2.3 (A), D3.3 (A), D4.3 (A), D5.3 (A), D6.3 (A), D7.3 (A), D19.P$1, D20.P$1, D21.P$1, D22.P$1, D23.P$1, D24.P$1, D25.P$1, D26.P$1, D28.3 (A), R23.1, R27.1, R31.1, R42.1, R44.1, R52.1, R59.1, SERIAL_TO_DAQ.1, SERIAL_TO_DAQ.2, SERIAL_TO_DAQ.39, SERIAL_TO_DAQ.40, TO_VI.5, TO_VI.6, TO_VI.9, U1.3 (VS-), U2.3 (VS-), U3.1 (GPIO2), U3.2 (GPIO3), U3.3 (REFM), U3.6 (AGND_2), U3.9 (AINM), U3.10 (AGND_3), U3.19 (AGND_4), U3.20 (AGND_5), U3.30 (AGND), U3.35 (BDGND), U3.37 (GPIO0), U3.38 (GPIO1), U4.1 (GPIO2), U4.2 (GPIO3), U4.3 (REFM), U4.6 (AGND_2), U4.9 (AINM), U4.10 (AGND_3), U4.19 (AGND_4), U4.20 (AGND_5), U4.30 (AGND), U4.35 (BDGND), U4.37 (GPIO0), U4.38 (GPIO1), U5.3 (VS-), U6.3 (VS-), U7.3 (VS-), U8.3 (VS-), U9.3 (VS-), U10.4 (GND); also elsewhere on the board
HES1: R56.2, TO_VI.1
HES1_SIGNAL: C38.1, D24.P$2, R56.1, U3.18 (CH8)
HES2: R54.2, TO_VI.2
HES2_SIGNAL: C37.1, D23.P$2, R54.1, U3.17 (CH9)
HES3: R49.2, TO_VI.3
HES3_SIGNAL: C36.1, D22.P$2, R49.1, U3.16 (CH10)
HES4: R47.2, TO_VI.4
HES4_SIGNAL: C35.1, D21.P$2, R47.1, U3.15 (CH11)
HES5: R58.2, TO_VI.7
HES5_SIGNAL: C39.1, D25.P$2, R58.1, U3.14 (CH12)
HES6: R60.2, TO_VI.8
HES6_SIGNAL: C40.1, D20.P$2, R60.1, U3.13 (CH13)
HES7: R61.2, TO_VI.10
HES7_SIGNAL: C41.1, D26.P$2, R61.1, U3.12 (CH14)
HES8: R62.2, TO_VI.11
HES8_SIGNAL: C42.1, D19.P$2, R62.1, U3.11 (CH15)
HES9: R41.2, TO_VI.12
HES9_SIGNAL: C30.1, D1.P$2, R41.1, U3.21 (CH7)
IN-: R34.1, R42.2, TT-L05.2
IN-1: R22.1, R23.2, TT-L04.2
IN-2: R26.1, R27.2, TT-L03.2
IN-3: R30.1, R31.2, TT-L02.2
IN-4: R40.1, R44.2, TT-L01.2
IN-5: R51.1, R52.2, TT-F02.2
IN-6: R57.1, R59.2, TT-F01.2
MBUS-SCL-1: SERIAL_TO_DAQ.4
MBUS-SDA-1: SERIAL_TO_DAQ.3
unnamed: U3.7 (MXO), U3.8 (AINP)
unnamed: U4.7 (MXO), U4.8 (AINP)
unnamed: C12.1, C23.2, R33.2, U1.8 (IN+)
unnamed: C12.2, C19.1, R34.2, U1.1 (IN-)
unnamed: D28.1 (VREF), D28.2 (C), R43.2, U1.2 (REF)
unnamed: C17.2, C18.1, R21.2, U2.8 (IN+)
unnamed: C16.1, C18.2, R22.2, U2.1 (IN-)
unnamed: D2.1 (VREF), D2.2 (C), R24.2, U2.2 (REF)
unnamed: C28.2, C29.1, R25.2, U5.8 (IN+)
unnamed: C21.1, C29.2, R26.2, U5.1 (IN-)
unnamed: D3.1 (VREF), D3.2 (C), R28.2, U5.2 (REF)
unnamed: C44.2, C48.1, R29.2, U6.8 (IN+)
unnamed: C34.1, C48.2, R30.2, U6.1 (IN-)
unnamed: D4.1 (VREF), D4.2 (C), R32.2, U6.2 (REF)
unnamed: C56.2, C57.1, R39.2, U7.8 (IN+)
unnamed: C55.1, C57.2, R40.2, U7.1 (IN-)
unnamed: D5.1 (VREF), D5.2 (C), R48.2, U7.2 (REF)
unnamed: C60.2, C61.1, R50.2, U8.8 (IN+)
unnamed: C59.1, C61.2, R51.2, U8.1 (IN-)
unnamed: D6.1 (VREF), D6.2 (C), R53.2, U8.2 (REF)
unnamed: C64.2, C65.1, R55.2, U9.8 (IN+)
unnamed: C63.1, C65.2, R57.2, U9.1 (IN-)
unnamed: D7.1 (VREF), D7.2 (C), R63.2, U9.2 (REF)
SEN_TBD0: U4.28 (CH0); also elsewhere on the board
SEN_TBD1: U4.27 (CH1); also elsewhere on the board
SEN_TBD2: U4.26 (CH2); also elsewhere on the board
SEN_TBD3: U4.25 (CH3); also elsewhere on the board
SEN_TBD4: U4.24 (CH4); also elsewhere on the board
SEN_TBD5: U4.23 (CH5); also elsewhere on the board
SEN_TBD6: U4.22 (CH6); also elsewhere on the board
SEN_TBD8: U4.18 (CH8); also elsewhere on the board
SEN_TBD9: U4.17 (CH9); also elsewhere on the board
SEN_TBD10: U4.16 (CH10); also elsewhere on the board
SEN_TBD11: U4.15 (CH11); also elsewhere on the board
SEN_TBD12: U4.14 (CH12); also elsewhere on the board
SEN_TBD13: U4.13 (CH13); also elsewhere on the board
SEN_TBD14: U4.12 (CH14); also elsewhere on the board
TT-F01: R55.1, TT-F01.1
TT-F01_SIGNAL: U3.28 (CH0), U9.5 (SENSE), U9.6 (OUT)
TT-F02: R50.1, TT-F02.1
TT-F02_SIGNAL: U3.27 (CH1), U8.5 (SENSE), U8.6 (OUT)
TT-L01: R39.1, TT-L01.1
TT-L01_SIGNAL: U3.26 (CH2), U7.5 (SENSE), U7.6 (OUT)
TT-L02: R29.1, TT-L02.1
TT-L03: R25.1, TT-L03.1
TT-L03_SIGNAL: U3.24 (CH4), U5.5 (SENSE), U5.6 (OUT)
TT-L04: R21.1, TT-L04.1
TT-L04_SIGNAL: U2.5 (SENSE), U2.6 (OUT), U3.23 (CH5)
TT-L05: R33.1, TT-L05.1
TT-L05_SIGNAL: U1.5 (SENSE), U1.6 (OUT), U3.22 (CH6)
TT-LO2_SIGNAL: U3.25 (CH3), U6.5 (SENSE), U6.6 (OUT)
V5D: SERIAL_TO_DAQ.5, SERIAL_TO_DAQ.6
V+: C68.1, U3.4 (REFP), U4.4 (REFP), U10.6 (VOUT)

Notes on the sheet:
Temperature via Thermocouple
-220 C
-40-25 C
Valve Position Sensors
K-Type Range = -180°C to 1200°C
With a Single 5V Supply:
1.24V REF = -248°C to 752°C
0.9V REF = -180°C to 820°C
0V REF = 0°C to 1000°C
ADCs to DAQ
All analog sensors go into the ADCs then are sent using SPI to the marionette data bus.
Temperature = (Vout - 1.25) / 0.005 V. So, for example, if the voltage is 1.5VDC, the temperature is (1.5 - 1.25) / 0.005 = 50°C
0V signal indicates the valves default position. 3.3V signal indicates the valves non-default position.



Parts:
C70, C71, C73, C74, C75, C76, C77, C78, C79, C80, C83, C84, C85, C86: 120pF; C0603K; MPN CL10C121JB8NNNC
D32, D33, D34, D35, D36, D37, D38, D39, D41, D42, D44, D45, D46, D47: D5V0H1U2LP1610-7; 0603DIODE; MPN D5V0H1U2LP1610-7
JP1: PINHD-2X12; 2X12; MPN PRPC012DAAN-RC
R65, R66, R68, R70, R71, R72, R73, R74, R78, R79, R88, R89, R90, R91: 1k; .0603-A-NOSILK; MPN ERJ-PA3F1001V

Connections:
GND: C70.2, C71.2, C73.2, C74.2, C75.2, C76.2, C77.2, C78.2, C79.2, C80.2, C83.2, C84.2, C85.2, C86.2, D32.P$1, D33.P$1, D34.P$1, D35.P$1, D36.P$1, D37.P$1, D38.P$1, D39.P$1, D41.P$1, D42.P$1, D44.P$1, D45.P$1, D46.P$1, D47.P$1; also elsewhere on the board
SEN0: JP1.1, R90.2
SEN1: JP1.2, R89.2
SEN2: JP1.3, R88.2
SEN3: JP1.5, R91.2
SEN4: JP1.9, R78.2
SEN5: JP1.11, R79.2
SEN7: JP1.15, R74.2
SEN8: JP1.18, R66.2
SEN9: JP1.17, R65.2
SEN10: JP1.19, R73.2
SEN11: JP1.21, R68.2
SEN12: JP1.22, R70.2
SEN13: JP1.23, R71.2
SEN14: JP1.24, R72.2
SEN_TBD0: C85.1, D46.P$2, R90.1; also elsewhere on the board
SEN_TBD1: C84.1, D45.P$2, R89.1; also elsewhere on the board
SEN_TBD2: C83.1, D44.P$2, R88.1; also elsewhere on the board
SEN_TBD3: C86.1, D47.P$2, R91.1; also elsewhere on the board
SEN_TBD4: C79.1, D41.P$2, R78.1; also elsewhere on the board
SEN_TBD5: C80.1, D42.P$2, R79.1; also elsewhere on the board
SEN_TBD6: C78.1, D39.P$2, R74.1; also elsewhere on the board
SEN_TBD8: C71.1, D33.P$2, R66.1; also elsewhere on the board
SEN_TBD9: C70.1, D32.P$2, R65.1; also elsewhere on the board
SEN_TBD10: C77.1, D38.P$2, R73.1; also elsewhere on the board
SEN_TBD11: C73.1, D34.P$2, R68.1; also elsewhere on the board
SEN_TBD12: C74.1, D35.P$2, R70.1; also elsewhere on the board
SEN_TBD13: C75.1, D36.P$2, R71.1; also elsewhere on the board
SEN_TBD14: C76.1, D37.P$2, R72.1; also elsewhere on the board

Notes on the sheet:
Valve Position Sensors
0V signal indicates the valves default position. 3.3V signal indicates the valves non-default position.

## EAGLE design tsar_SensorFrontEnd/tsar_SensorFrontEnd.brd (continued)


Board: 2 copper layers, 93.3 x 94.9 mm, 261 parts (0 on the bottom side), 146 nets.

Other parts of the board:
U$5: PSAS_LOGO_10X10

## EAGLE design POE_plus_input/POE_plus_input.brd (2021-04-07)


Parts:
BBAI_5V: PINHD-1X2; 1X02; MPN 1718573002
BOOST_CAP: 0.01uF; C0805K; MPN 06035C103JAT2A
C_IN1, C_IN2: 15uF/50V; C2220K; MPN KTS500B156M55N0T00
C_IN3: 0.47uF; C0805K; MPN UMK107ABJ474KA-T
C_OUT: 47uF/16V; C1210K; MPN GRM32EC81C476KE15K
C_OUT1: 100uF/16V; C1210K; MPN EMK325ABJ107MM-P
C_OUT2: 33uF/16V; C1206K; MPN C3216X5R1C336M160AB
D1: SR305; C4111-15; MPN SR305-TP
H1, H2, H3, H4, H5, H6, H7, H8: #4-BARE_MOUNTING_HOLE/.300; #4/.300-BARE+STD_NUT_OR_STAR_WASHER
I_LIM_ADJ: 8.2k; 1206-A; MPN RC1206FR-078K2L
L1: 33uH; L_SHIELDED_13MMX13MMX6MM; MPN PE-53823SNL
PIT_GREEN: PINHD-1X2; 1X02; MPN 1718573002
POE_IN: 24V; DCJACK_2MM_SMT; MPN KLDX-SMT2-0202-ATR
SFE_5V, SFE_24V: PINHD-1X2; 1X02; MPN 1718573002
SOFTSTART: 1nF; C0603K; MPN CL10C102JB8NNNC
U1: LM2673SX-5.0/NOPB; TS7B; MPN LM2673SX-5.0/NOPB
VI_24V: PINHD-1X2; 1X02; MPN 1718573002

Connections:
+5V: BBAI_5V.1, C_OUT.1, C_OUT1.1, C_OUT2.1, L1.2, SFE_5V.1, U1.6 (FB)
+24V: C_IN1.1, C_IN2.1, C_IN3.1, PIT_GREEN.1, POE_IN.PWR1 (PWR), SFE_24V.1, U1.2 (VIN), VI_24V.1
GND: BBAI_5V.2, C_IN1.2, C_IN2.2, C_IN3.2, C_OUT.2, C_OUT1.2, C_OUT2.2, D1.A, I_LIM_ADJ.1, PIT_GREEN.2, POE_IN.GND (GNDBREAK), POE_IN.GNDBREAK (GND), SFE_5V.2, SFE_24V.2, SOFTSTART.2, U1.4 (GND), U1.8 (TAB), VI_24V.2
unnamed: SOFTSTART.1, U1.7 (SS)
unnamed: BOOST_CAP.2, D1.C, L1.1, U1.1 (SW)
unnamed: I_LIM_ADJ.2, U1.5 (ADJ)
unnamed: BOOST_CAP.1, U1.3 (CB)

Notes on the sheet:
Drill Holes for Standoffs.


Board: 2 copper layers, 93.3 x 95.1 mm, 27 parts (0 on the bottom side), 7 nets.

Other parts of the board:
U$5: PSAS_LOGO_10X10

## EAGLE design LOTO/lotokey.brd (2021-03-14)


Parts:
C1, C2, C4, C5, C7, C8, C10, C11, C13, C14, C16, C17, C19, C20, C22, C23, C25, C26: 4.7uF/25V; C050-025X075; MPN FG28X5R1E475KRT06
C3, C6, C9, C12, C15, C18, C21, C24, C27: 10uF; C050-025X075; MPN FG28X5R1E106MRT06
GREEN, GREEN1, GREEN2, GREEN3, GREEN4, GREEN5, GREEN6, GREEN7, GREEN8: TLLR4400; LED3MM; MPN TLHG5200
JP1, JP2, JP3, JP4, JP5, JP6, JP7, JP8, JP9, JP10: PINHD-1X2; 1X02; MPN OSTVN02A150
JP11: PINHD-1X12; 1X12; MPN 1-640454-2
L1, L2, L3, L4, L5, L6, L7, L8, L9: 6.8uH; 0204/5; MPN B78108S1682K000
NMOS, NMOS1, NMOS2, NMOS3, NMOS4, NMOS5, NMOS6, NMOS7, NMOS8: BSS296; TO92; MPN 2N7000-G
PMOS, PMOS1, PMOS2, PMOS3, PMOS4, PMOS5, PMOS6, PMOS7, PMOS8: BSS110; TO92; MPN TP2104N3-G
PS1, PS2, PS3, PS4, PS5, PS6, PS7, PS8, PS9: PDSE1-S5-S5-S; CONV_PDSE1-S5-S5-S; MPN PDSE1-S5-S5-S
R1, R3, R4, R6, R7, R9, R10, R12, R13, R15, R16, R18, R19, R21, R22, R24, R25, R27: 1k; 0204/7; MPN CCF551K00FKE36
R2, R5, R8, R11, R14, R17, R20, R23, R26: 10k; 0204/7; MPN CCF5510K0FKE36
RED, RED1, RED2, RED3, RED4, RED5, RED6, RED7, RED8: TLLR4400; LED3MM; MPN TLUR6400

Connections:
+5V: C1.1, C4.1, C7.1, C10.1, C13.1, C16.1, C19.1, C22.1, C25.1, JP1.1, JP11.1, L1.1, L2.1, L3.1, L4.1, L5.1, L6.1, L7.1, L8.1, L9.1
GND: C1.2, C2.2, C3.2, C4.2, C5.2, C6.2, C7.2, C8.2, C9.2, C10.2, C11.2, C12.2, C13.2, C14.2, C15.2, C16.2, C17.2, C18.2, C19.2, C20.2, C21.2, C22.2, C23.2, C24.2, C25.2, C26.2, C27.2, JP1.2, JP11.2, JP11.3, NMOS.3 (S), NMOS1.3 (S), NMOS2.3 (S), NMOS3.3 (S), NMOS4.3 (S), NMOS5.3 (S), NMOS6.3 (S), NMOS7.3 (S), NMOS8.3 (S), PS1.1 (GND), PS1.3 (0V), PS2.1 (GND), PS2.3 (0V), PS3.1 (GND), PS3.3 (0V), PS4.1 (GND), PS4.3 (0V), PS5.1 (GND), PS5.3 (0V), PS6.1 (GND), PS6.3 (0V), PS7.1 (GND), PS7.3 (0V), PS8.1 (GND), PS8.3 (0V), PS9.1 (GND), PS9.3 (0V), R2.2, R5.2, R8.2, R11.2, R14.2, R17.2, R20.2, R23.2, R26.2, RED.K (C), RED1.K (C), RED2.K (C), RED3.K (C), RED4.K (C), RED5.K (C), RED6.K (C), RED7.K (C), RED8.K (C)
unnamed: C2.1, L1.2, PS1.2 (VIN)
unnamed: R1.2, RED1.A
unnamed: GREEN.K (C), NMOS.2 (D)
unnamed: GREEN.A, R3.2
unnamed: PMOS1.1 (S), R1.1
unnamed: C5.1, L2.2, PS2.2 (VIN)
unnamed: GREEN1.K (C), NMOS1.2 (D)
unnamed: R4.2, RED.A
unnamed: PMOS.1 (S), R4.1
unnamed: GREEN1.A, R6.2
unnamed: R7.2, RED2.A
unnamed: PMOS2.1 (S), R7.1
unnamed: C8.1, L3.2, PS3.2 (VIN)
unnamed: GREEN2.K (C), NMOS2.2 (D)
unnamed: GREEN2.A, R9.2
unnamed: R10.2, RED3.A
unnamed: PMOS3.1 (S), R10.1
unnamed: C11.1, L4.2, PS4.2 (VIN)
unnamed: GREEN3.K (C), NMOS3.2 (D)
unnamed: GREEN3.A, R12.2
unnamed: R13.2, RED4.A
unnamed: PMOS4.1 (S), R13.1
unnamed: C14.1, L5.2, PS5.2 (VIN)
unnamed: GREEN4.K (C), NMOS4.2 (D)
unnamed: GREEN4.A, R15.2
unnamed: R16.2, RED5.A
unnamed: PMOS5.1 (S), R16.1
unnamed: C17.1, L6.2, PS6.2 (VIN)
unnamed: GREEN5.K (C), NMOS5.2 (D)
unnamed: GREEN5.A, R18.2
unnamed: R19.2, RED6.A
unnamed: PMOS6.1 (S), R19.1
unnamed: C20.1, L7.2, PS7.2 (VIN)
unnamed: GREEN6.K (C), NMOS6.2 (D)
unnamed: GREEN6.A, R21.2
unnamed: R22.2, RED7.A
unnamed: PMOS7.1 (S), R22.1
unnamed: C23.1, L8.2, PS8.2 (VIN)
unnamed: GREEN7.K (C), NMOS7.2 (D)
unnamed: GREEN7.A, R24.2
unnamed: R25.2, RED8.A
unnamed: PMOS8.1 (S), R25.1
unnamed: C26.1, L9.2, PS9.2 (VIN)
unnamed: GREEN8.K (C), NMOS8.2 (D)
unnamed: GREEN8.A, R27.2
SWITCH1: C3.1, JP2.1, PMOS.3 (D), PS1.4 (+VOUT), R3.1
SWITCH2: C6.1, JP3.1, PMOS1.3 (D), PS2.4 (+VOUT), R6.1
SWITCH3: C9.1, JP4.1, PMOS2.3 (D), PS3.4 (+VOUT), R9.1
SWITCH4: C18.1, JP5.1, PMOS5.3 (D), PS6.4 (+VOUT), R18.1
SWITCH5: C15.1, JP6.1, PMOS4.3 (D), PS5.4 (+VOUT), R15.1
SWITCH6: C12.1, JP7.1, PMOS3.3 (D), PS4.4 (+VOUT), R12.1
SWITCH7: C27.1, JP8.1, PMOS8.3 (D), PS9.4 (+VOUT), R27.1
SWITCH8: C24.1, JP9.1, PMOS7.3 (D), PS8.4 (+VOUT), R24.1
SWITCH9: C21.1, JP10.1, PMOS6.3 (D), PS7.4 (+VOUT), R21.1
SW_SIG1: JP2.2, JP11.5, NMOS.1 (G), PMOS.2 (G), R5.1
SW_SIG2: JP3.2, JP11.4, NMOS1.1 (G), PMOS1.2 (G), R2.1
SW_SIG3: JP4.2, JP11.12, NMOS2.1 (G), PMOS2.2 (G), R8.1
SW_SIG4: JP5.2, JP11.10, NMOS5.1 (G), PMOS5.2 (G), R17.1
SW_SIG5: JP6.2, JP11.8, NMOS4.1 (G), PMOS4.2 (G), R14.1
SW_SIG6: JP7.2, JP11.6, NMOS3.1 (G), PMOS3.2 (G), R11.1
SW_SIG7: JP8.2, JP11.11, NMOS8.1 (G), PMOS8.2 (G), R26.1
SW_SIG8: JP9.2, JP11.9, NMOS7.1 (G), PMOS7.2 (G), R23.1
SW_SIG9: JP10.2, JP11.7, NMOS6.1 (G), PMOS6.2 (G), R20.1

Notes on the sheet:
5V DC supply from main battery
There is a key switch on the terminal block. When the switch is in the 'ON' position this circuit will light up the GREEN LED only. When the switch is in the 'OFF' position, this circuit will light up the RED LED only.
Switch Signal 2 pin from key
Switch Signal 1 pin from key


Board: 2 copper layers, 167.4 x 190.5 mm, 119 parts (0 on the bottom side), 65 nets.

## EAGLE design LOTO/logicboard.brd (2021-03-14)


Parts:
D1, D2: CGRM4001-G; SOD-123_MINI-SMA; MPN CMHSH5-4 TR PBFREE
E_STOP: PINHD-1X2; 1X02; MPN OSTVN02A150
H1, H2, H3, H4: MOUNT-HOLE2.8; 2,8
JP1: PINHD-1X12; 1X12; MPN 1-640454-2
POE+_INJ: PINHD-1X2; 1X02; MPN 0022232021
POE+_PS: PINHD-1X2; 1X02; MPN OSTVN02A150
POE_INJ: PINHD-1X2; 1X02; MPN 0022232021
Q1, Q4: 220mA/50V/3.5Ω; SOT23-3; MPN BSS138P,215
Q2, Q3: IRF9530; TO220BV; MPN IRF9530NPBF
R1, R3: 4.7K; .0805-C-NOSILK; MPN RC0805FR-074K7L
R12, R16: 10k; .0805-C-NOSILK; MPN RC0805FR-0710KL
R13, R21: 28k; .0805-C-NOSILK; MPN RMCF0805FT28K0
R_S1, R_S2, R_S3, R_S4, R_S5, R_S6, R_S7, R_S8, R_S9: 1k; .0603-C-NOSILK; MPN ERJ-PA3F1001V
U1, U2: CD4082BNSR; NS14; MPN CD4082BNSR

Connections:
+5V: JP1.1, U1.14 (VDD), U2.14 (VDD)
GND: E_STOP.2, JP1.2, JP1.3, POE+_INJ.2, POE+_PS.2, POE_INJ.2, Q1.2 (S), Q4.2 (S), R12.1, R13.1, R16.1, R21.1, U1.7 (VSS), U2.7 (VSS)
unnamed: JP1.4, R_S8.1
unnamed: JP1.5, R_S4.1
unnamed: JP1.6, R_S7.1
unnamed: JP1.7, R_S3.1
unnamed: JP1.8, R_S2.1
unnamed: JP1.9, R_S1.1
unnamed: JP1.10, R_S6.1
unnamed: JP1.11, R_S9.1
unnamed: JP1.12, R_S5.1
unnamed: Q1.3 (D), Q2.G, R1.1
unnamed: U1.5 (A), U2.1 (J)
unnamed: U1.13 (K), U2.5 (A)
unnamed: D1.A, R13.2
unnamed: Q3.G, Q4.3 (D), R3.1
unnamed: D2.A, R21.2
ON: Q1.1 (G), Q4.1 (G), R12.2, R16.2, U1.1 (J)
S1: R_S1.2, U1.4 (B)
S2: R_S2.2, U1.3 (C)
S3: R_S3.2, U1.2 (D)
S4: R_S4.2, U2.3 (C)
S5: R_S5.2, U1.9 (E)
S6: R_S6.2, U1.11 (G), U1.12 (H)
S7: R_S7.2, U2.4 (B)
S8: R_S8.2, U2.2 (D)
S9: R_S9.2, U1.10 (F)
SOL_GPIO_1: D1.C, POE_INJ.1, Q3.D
SOL_GPIO_10: D2.C, POE+_INJ.1, Q2.D
VCC: E_STOP.1, Q3.S, R3.2
VDD: POE+_PS.1, Q2.S, R1.2

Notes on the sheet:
Main Logic
Power Inputs
This circuit is triggered by the logic output. If 'on' the power from the POE+ (power switch) will be connected, if 'off' the POE+ injector will be off.
This circuit is triggered by the logic output. If 'on' the power from the POE (e-stop) will be connected, if 'off' the POE injector will be off.
These are the three power inputs. The POE+_PS is from the POE+ Power Switch. The E_STOP is from the emergency stop button. The 5V USB power goes into the Main Logic input header. The switches are connected to the POE injectors respective power supplies.
This circuit has the 9 key switch inputs going into AND logic gates. Only when all 9 key switches are in the LOTO box and turned does the logic signal send a logic 'on' trigger.


Board: 2 copper layers, 58.4 x 41.6 mm, 32 parts (0 on the bottom side), 31 nets.

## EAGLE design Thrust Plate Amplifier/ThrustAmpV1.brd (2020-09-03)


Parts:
C1: 4.7 uF; C0805; MPN CL21A475KAQNNNE
C2: 100 nF; C0805; MPN 08055D104KAT2A
C3: 22 uF; C0805; MPN CL21A226KPCLRNC
C4, C11: 10 nF; C0805; MPN C2012X5R2E103K125AA
C5, C12: 1 uF; C0805; MPN CL21A105KACLNNC
C6, C13: 2.2 uF; C0805; MPN CL21A225KAFNNNG
C7, C8, C9, C10, C19, C20, C22: 100 nF; C0805K; MPN 08055D104KAT2A
C14, C15, C16, C17: 120 pF; C0805; MPN C0805C121KDRACTU
C18, C23, C24, C25, C26, C27, C28, C29: 100 pF; C0805K; MPN 885012207054
CR1: 1N4148W-7-F; SOD123; MPN 1N4148W-7-F
D1: 10BQ060TR; SMB; MPN 10BQ060TR
D2, D3, D4, D5, D6, D7, D8, D10, D11, D12, D13, D14, D15, D16: D5V0H1U2LP1610-7; 0603DIODE; MPN D5V0H1U2LP1610-7
D9: D12V0H1U2LP1610-70603DIODE12V; 0603DIODE; MPN D12V0H1U2LP1610-7
H5, H6, H7, H8: #4-BARE_MOUNTING_HOLE/.300; #4/.300-BARE+STD_NUT_OR_STAR_WASHER
J1: CONN_02PTH3; 1X02_LONGPADS; MPN 22232021
J2: CONN_05PTH_LONGPADS; 1X05_LONGPADS; MPN 0022232051
J4, J5, J6, J7: CONN_04; 1X04; MPN 0022232041
R1, R2, R3, R4: TBD; R0805
R5, R6, R7, R8, R9, R10, R11, R12: NP; 0207/5V
R13, R18, R19, R20: 1 K; R0805; MPN RC0805FR-071KL
R14: 19.1 k; R0805; MPN RNCP0805FTD19K1
R15: NP; R0805
R16: 124k; R0805; MPN RK73H2ATTD1243F
R17: 499 k; R0805; MPN RK73H2ATTD4993F
TP1, TP2, TP3, TP4: TEST-POINTTP_15TH_THRU; TP_15TH
U1, U2, U3, U4: INA126PA; P8; MPN INA126PA
U5: LP2985AIM5-3.3; MF05A; MPN LP2985AIM5-3.3/NOPB
U6: LP2985AIM5-5.0/NOPB; MF05A; MPN LP2985AIM5-5.0/NOPB
U$1: MP2456GJ-P; SOT6; MPN MP2456GJ-P
U$2: CLF5030NIT-100M-D; 0.209"LX0.197"W(5.30MMX5.00MM); MPN CLF5030NIT-100M-D

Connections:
3.3V: C7.1, C8.1, C9.1, C10.1, C13.1, TP4.P$1, U1.7 (V+), U2.7 (V+), U3.7 (V+), U4.7 (V+), U5.5 (VOUT)
5V: C6.1, C12.1, C19.1, C20.1, D15.P$2, D16.P$2, J4.1, J5.1, J6.1, J7.1, R5.1, R6.1, R7.1, R8.1, R9.1, R10.1, R11.1, R12.1, TP3.P$1, U5.1 (VIN), U5.3 (ON), U6.5 (VOUT)
6V: C3.1, C5.1, CR1.2, R16.2, TP2.P$1, U6.1 (VIN), U6.3 (ON), U$2.2
12V: C1.1, C22.1, D9.P$2, J1.2, R17.2, TP1.P$1, U$1.P$5 (IN)
GND: C1.2, C3.2, C4.2, C5.2, C6.2, C7.2, C8.2, C9.2, C10.2, C11.2, C12.2, C13.2, C14.2, C15.1, C16.1, C17.2, C18.2, C19.2, C20.2, C22.2, C23.2, C24.2, C25.2, C26.2, C27.2, C28.2, C29.2, D1.A, D2.P$1, D3.P$1, D4.P$1, D5.P$1, D6.P$1, D7.P$1, D8.P$1, D9.P$1, D10.P$1, D11.P$1, D12.P$1, D13.P$1, D14.P$1, D15.P$1, D16.P$1, J1.1, J2.5, J4.4, J5.4, J6.4, J7.4, R14.1, R15.2, U1.4 (V-), U1.5 (REF), U2.4 (V-), U2.5 (REF), U3.4 (V-), U3.5 (REF), U4.4 (V-), U4.5 (REF), U5.2 (GND), U6.2 (GND), U$1.P$2 (GND)
unnamed: R1.2, U1.8 (RG)
unnamed: R1.1, U1.1 (RG_2)
unnamed: R2.2, U2.8 (RG)
unnamed: R2.1, U2.1 (RG_2)
unnamed: R3.2, U3.8 (RG)
unnamed: R3.1, U3.1 (RG_2)
unnamed: R4.2, U4.8 (RG)
unnamed: R4.1, U4.1 (RG_2)
unnamed: R14.2, R16.1, U$1.P$3 (FB)
unnamed: C2.1, CR1.1, U$1.P$1 (BST)
unnamed: R13.2, U1.6 (VO)
unnamed: R18.2, U2.6 (VO)
unnamed: R19.1, U3.6 (VO)
unnamed: R20.1, U4.6 (VO)
unnamed: C16.2, D5.P$2, J2.1, R13.1
unnamed: C15.2, D6.P$2, J2.2, R18.1
unnamed: C2.2, D1.C, U$1.P$6 (SW), U$2.1
unnamed: C14.1, D3.P$2, J2.3, R19.2
unnamed: C17.1, D4.P$2, J2.4, R20.2
unnamed: C11.1, U5.4 (BP)
unnamed: C4.1, U6.4 (BP)
unnamed: R15.1, R17.1, U$1.P$4 (EN)
unnamed: C18.1, D11.P$2, J4.2, R5.2, U1.3 (V+IN)
unnamed: C26.1, D10.P$2, J4.3, R6.2, U1.2 (V-IN)
unnamed: C23.1, D12.P$2, J5.2, R7.2, U2.3 (V+IN)
unnamed: C27.1, D8.P$2, J5.3, R8.2, U2.2 (V-IN)
unnamed: C24.1, D13.P$2, J6.2, R9.2, U3.3 (V+IN)
unnamed: C28.1, D7.P$2, J6.3, R10.2, U3.2 (V-IN)
unnamed: C25.1, D14.P$2, J7.2, R11.2, U4.3 (V+IN)
unnamed: C29.1, D2.P$2, J7.3, R12.2, U4.2 (V-IN)

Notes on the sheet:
Thrust Plate Power Supply: 5V
Amplifier Power Supply: 3.3 V
Thrust Plate Connector and Bridge Biasing Resistors
Data Out
Thrust Plate Amplifier and Power Supply Board
Designed by Mike Hall for 2019-2020 TSAR ECE Capstone
Step-Down Switching Regulator (6V)
Power In (12 V)
All resistors are 0805 1% unless otherwise specified. All capacitors are 0805 10% X5R with working voltage 25 V unless otherwise specified.


Board: 2 copper layers, 101.6 x 76.2 mm, 87 parts (0 on the bottom side), 35 nets.

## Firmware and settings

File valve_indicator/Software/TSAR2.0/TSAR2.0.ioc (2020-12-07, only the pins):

Mcu.UserName=STM32F042K6Ux
PA0.GPIO_Label=Hall Effect Sensor Nine
PA0.Signal=GPIO_Input
PA1.GPIO_Label=Hall Effect Sensor One
PA1.Signal=GPIO_Input
PA15.GPIO_Label=Hall Effect Sensor Seven
PA15.Signal=GPIO_Input
PA2.GPIO_Label=Hall Effect Sensor Two
PA2.Signal=GPIO_Input
PA3.GPIO_Label=Hall Effect Sensor Three
PA3.Signal=GPIO_Input
PA4.GPIO_Label=Hall Effect Sensor Four
PA4.Signal=GPIO_Input
PA5.Signal=SPI1_SCK
PA6.Signal=SPI1_MISO
PA7.Signal=SPI1_MOSI
PA8.GPIO_Label=Hall Effect Sensor Eight
PA8.Signal=GPIO_Input
PB0.GPIO_Label=Buzzer
PB0.Signal=GPIO_Output
PB1.GPIO_Label=SD_CS
PB1.Signal=GPIO_Output
PB3.GPIO_Label=LED Three
PB3.Signal=GPIO_Output
PB4.GPIO_Label=LED Two
PB4.Signal=GPIO_Output
PB5.GPIO_Label=LED One
PB5.Signal=GPIO_Output
PB6.GPIO_Label=Hall Effect Sensor Six
PB6.Signal=GPIO_Input
PB7.GPIO_Label=Hall Effect Sensor Five
PB7.Signal=GPIO_Input

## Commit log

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2020-04-23 Add files via upload
    Schematic missing connections to printer cable headers.
    [tsar_SensorFrontEnd.brd, tsar_SensorFrontEnd.sch]
2020-04-23 Add files via upload
    Added AC Eagle Files to the New Locale!
    [TSAR_Actuator_Controller.brd, TSAR_Actuator_Controller.sch]
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2020-04-23 some changes from Andrew during design review (now with supplies).
    [tsar_SensorFrontEnd.brd, tsar_SensorFrontEnd.sch]
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2020-04-23 Resized Schematic Frame Added connectors for Thrust Plate Input Amp Added 3v3 Regulator (missing resistor values set to TBD)
    [tsar_SensorFrontEnd.brd, tsar_SensorFrontEnd.sch]
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2020-04-26 Reduced board size
    fixed missing TVS cap values
    modified board layout to reduce size
    [tsar_SensorFrontEnd.brd, tsar_SensorFrontEnd.sch]
2020-04-28 Shrunk Board Layout
    Reduced size of board
    Replaced 20x2 connectors with marionette library part.
    Missing digital pin connections
    [tsar_SensorFrontEnd.brd, tsar_SensorFrontEnd.sch]
2020-04-28 Labeled pressure/temp sensor limits Moved ADS pins in schematic Missing digital pin connections
    [tsar_SensorFrontEnd.brd, tsar_SensorFrontEnd.sch]
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2020-04-30 changed wire size
    replaced 0603 resistors with 0805
    replaced thrust plate 4 pin connector with 6 pin
    missing digital connections
    missing mounting holes
    tvs diodes need to be replaced
    [tsar_SensorFrontEnd.brd, tsar_SensorFrontEnd.sch]
2020-05-05 THE PENULTIMATE AMPLIFIER
    ALMOST ready for OSHpark. Just a few minor chores left.
    [ThrustAmpV1.brd, ThrustAmpV1.sch]
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2020-05-07 I broke everything
    [tsar_SensorFrontEnd.brd, tsar_SensorFrontEnd.sch]
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2020-05-09 More ADC channels usable
    Added circuitry with jumpers for the remaining 3 channels on the ADS8344.
    Changed to 5V 0603 TVS diodes.
    Added 2 pin 12V out connector for Thrust Plate Amp
    [tsar_SensorFrontEnd.brd, tsar_SensorFrontEnd.sch]
2020-05-10 THE ACTUAL ULTIMATE AMPLIFIER
    Made all changes from the last design review. Added test points. Fixed isolation. Fixed TVS diode placement. Added proper mounting holes.
    Also adjusted all names on top silkscreen so they're legible and don't overlap.
    [ThrustAmpV1.brd, ThrustAmpV1.sch]
2020-05-10 THE ACTUAL ULTIMATE AMPLIFIER
    Made all changes from the last design review. Added test points. Fixed isolation. Fixed TVS diode placement. Added proper mounting holes. Also adjusted all names on top silkscreen so they're legible and don't overlap. Suspect board is ready for fab.
    [ThrustAmpV1.brd, ThrustAmpV1.sch]
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2020-05-10 Added BOM for thrust plate amp
    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
    [BOMplateamp.xlsx, ThrustAmpV1.brd]
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2020-05-12 Replaced Resistors and 5V TVS Diodes.
    Changed resistors to 0805 to be the same size as the caps.
    Changed to a standard sized TVS Diode footprint.
    Began Board layouts.
    [TSAR_Actuator_Controller.brd, TSAR_Actuator_Controller.sch]
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2020-05-17 Added Second ADS8344
    Second ADS8344 on schematic
    Board Layout horribly broken
    [tsar_SensorFrontEnd.brd, tsar_SensorFrontEnd.sch]
2020-05-18 Second ADS8344 layout and routing
    Layed out and routed circuits for second ADC chip
    Changed Analog connections to be more compact
    Increased size of board, vert and horz
    [tsar_SensorFrontEnd.brd, tsar_SensorFrontEnd.sch]
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2020-05-26 Last Minute Fixes.
    Corrected Morpho Connector Spacing.
    Made all traces min 10 mil.
    [TSAR_Actuator_Controller.brd, TSAR_Actuator_Controller.sch]
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2020-05-26 Last minutes silk screen fixes.
    [TSAR_Actuator_Controller.brd, TSAR_Actuator_Controller.sch]
2020-05-26 Polishing
    Moved to multiple sheets
    Font changed to vector
    resized part names and moved to be visible
    [tsar_SensorFrontEnd.brd, tsar_SensorFrontEnd.sch]
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2020-05-26 Corrected Morpho Connector Position Again.
    [TSAR_Actuator_Controller.brd]
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2020-05-26 Changed Voltage Regulator Layout
    Added Bill of Materials
    Added Digikey BOM csv for easy import
    Enlarged Text
    Added Values to all diodes
    [DigikeyBOM.csv, tsar_SensorFrontEnd.brd, tsar_SensorFrontEnd.sch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]
2020-05-26 Wrong Date on board
    [tsar_SensorFrontEnd.brd]
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2020-09-04 Attributes for Sensor Front End Board
    Added attributes to components for BOM generation on SFE board.
    Old bill of material files moved to subfolder
    [DigikeyBOM.csv, tsar_SensorFrontEnd.brd, tsar_SensorFrontEnd.csv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]
2020-09-05 Fixed Inconsistency Error
    exported BOM isn't grouping like parts correctly
    [tsar_SensorFrontEnd.brd, tsar_SensorFrontEnd.csv, tsar_SensorFrontEnd.sch]
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2020-09-22 fixed attribute errors
    [TSAR_Actuator_Controller.brd, TSAR_Actuator_Controller.sch]
2020-09-29 Fixed inconsistency error in actuator controller board
    [TSAR_Actuator_Controller.brd, TSAR_Actuator_Controller.sch, test.csv]
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2020-12-27 final error checks
    [TSAR_Actuator_Controller.brd, tsar_SensorFrontEnd.brd, tsar_SensorFrontEnd.sch]
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2020-12-28 label correction
    [TSAR_Actuator_Controller.brd, tsar_SensorFrontEnd.brd]
2020-12-28 Minor cleanup around the SPS, minor polish on ground and on vbatt distribution.
    [TSAR_Actuator_Controller.brd, TSAR_Actuator_Controller.sch]
2020-12-29 bom, attributes, sizing, layout
    updated BOMs, changed smds from 0805 to 0603, updated attributes, changed layout to reduce overall board size.
    [tsar_SensorFrontEnd.brd, tsar_SensorFrontEnd.csv, tsar_SensorFrontEnd.sch]
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2021-01-15 replaces 4 caps with 1206 due to stock
    [tsar_SensorFrontEnd.brd, tsar_SensorFrontEnd.sch]
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2021-01-21 fixed text on tplace.
    [tsar_SensorFrontEnd.brd]
2021-01-30 ac, valve indicator, libraries
    ac-board: changed attribute.
    valve-indicator V1: upgraded processor, changed buck regs, added crystal, layed out all unused processor pins, added battery power sense, updated attributes, and re-layout of entire board.
    libraries: created custom library, added new libraries.
    [BOM.csv, BOM_valve_indicator.csv, TSAR_Actuator_Controller.brd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]
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2021-02-03 replaced ssop20 with correct package
    [tsar_SensorFrontEnd.brd, tsar_SensorFrontEnd.sch]
2021-02-20 poe/ac/sfe changes, libraries
    POE low risk input board created; will manage POE+ power distribution to subsystems. added 24-> 5v regulator for SFE and BB-AI
    added libraries for SFE and POE.
    SFE: removed 24->5V regulator from SFE, replaced D27&D31 with correct package, replaced ADC to correct SSOP20 package.
    AC: replaced all passives with oresat rcl parts
    [POE_plus_input.brd, POE_plus_input.sch, TSAR_Actuator_Controller.brd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]
2021-02-20 SFE/AC changes
    AC: began replacing nucleo with bare metal stm
    SFE: replaced all passives with oresal parts
    [TSAR_Actuator_Controller.brd, TSAR_Actuator_Controller.sch, tsar_SensorFrontEnd.brd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]
2021-02-21 board corrections following test case.
    issue #6 closed.
    [tsar_SensorFrontEnd.brd, tsar_SensorFrontEnd.sch]
2021-02-21 POE, Vi board changes
    POE Input Board: Added BB outline and mounting holes for BB-AI. Added small board standard outline and adjusted board size. Added attributes to regulator parts.
    Valve Indicator: Added small board standard outline and adjusted board size.
    [BeagleBone_Black_Wireless_Outline.dxf, POE_plus_input.brd, POE_plus_input.sch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]
2021-02-22 Vi changes
    Added SD card circuit. Added 9POS for sending position sensor data to the SFE board. Updated attributes.
    [valve_indicatorV1.brd, valve_indicatorV1.sch]
2021-02-22 Stnd outlines, Poe, SFE, Vi changes
    Added Standard Outline DXF files to separate folder
    POE Input Board: updated attributes, added BOM
    SFE: updated attributes, updated BOM
    Valve ind: layout changes, added attributes, updated BOM
    [BOM_valve_indicator.csv, BeagleBone_Black_Wireless_Outline.dxf, POE_plus_input.brd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]
2021-02-22 POE, SFE changes
    POE: added gnd vias and text info
    SFE: moved to mar dxf outline. removed unallocated lines and added valve position sensor pinout. updated attributes. the board is currently unrouted.
    [POE_plus_input.brd, tsar_SensorFrontEnd.brd, tsar_SensorFrontEnd.sch]
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2021-02-25 VI: updated attributes and layout
    Component lead time +1month, changed board for different parts.
    [valve_indicatorV1.brd, valve_indicatorV1.sch]
2021-02-26 Updated LOTO boards
    Added LOTO housing outline. Added logic for POE power and gate trigger. Added more circuit protection and power isolation.
    [LOTO.dxf, logicboard.brd, logicboard.sch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]
2021-03-02 AC changes. Added library
    AC: Replaced headers with STM32 processor. Began direct control connections. To Do: Need to add USB circuit. Update pinout for IDE.
    Library: added SPI compatible ADC for SFE board future revision.
    [TSAR_Actuator_Controller.brd, TSAR_Actuator_Controller.sch]
2021-03-14 LOTO, Library changes
    LOTO: added attributes to lotokey board and exported BOM. Updated parts to SMD, updated attributes, completed layout/routes, and exported BOM.
    Library: CD4082 SMD AND logic gate for LOTO board added.
    [logicboard.brd, logicboard.sch, logicboardBOM.csv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]
2021-03-18 POE, VI, and library changes
    POE Input: Corrected pad size, updated attributes, adjusted layout.
    Valve Indicator: Changed layout (sd card facing 'S').
    [POE_plus_input.brd, POE_plus_input.sch, valve_indicatorV1.brd]
2021-03-24 SFE changes
    Replaced ADC's with two 16 channel SPI
    [tsar_SensorFrontEnd.brd, tsar_SensorFrontEnd.sch]
2021-03-25 AC, SFE, Library Changes
    AC: Reverted to headers for Nucleo. Removed sensors (data coming over usb cable to nucleo), removed power regulator (power coming from usb cable). Replaced leds with correct size and attributes.
    SFE: Removed RTD/TVS circuits. Added thermocouple inputs and thermocouple amplifier circuit. Finished ADC wiring. Added schematic info annotations. Cleaned up schematic. TODO: change labels to consistent font/size. layout new components, complete attributes for new components.
    Library: Added oresat-rcl library.
    [TSAR_Actuator_Controller.brd, TSAR_Actuator_Controller.sch, tsar_SensorFrontEnd.brd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]
2021-04-03 AC, VI, library changes
    AC: attribute corrections
    VI: corrected MISO/MISI pins
    Library: Added REF5025 for ADCs on SFE board.
    [TSAR_Actuator_Controller.brd, TSAR_Actuator_Controller.sch, valve_indicatorV1.brd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]
2021-04-03 SFE Changes
    Added amplifier circuit for thermocouples. Added reference voltage for ADCs.
    [tsar_SensorFrontEnd.brd, tsar_SensorFrontEnd.sch]
2021-04-06 AC, SFE, VI changes
    AC: Added 5 pin header for sending UART status updates to the valve indicator board. Will only send the current test stand state status, so recieving data from the Vi. Routed header and added labels.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
    SFE: Routed thermocouple amps and ADCs. Made all labels consistent. Updated attributes and BOM.
    VI: Updated attributes and BOM.
    [BOM_valve_indicator.csv, TSAR_Actuator_Controller.brd, TSAR_Actuator_Controller.csv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]
2021-04-06 SFE, VI changes
    SFE: cleared errors
    VI: cleared errors
    [tsar_SensorFrontEnd.brd, tsar_SensorFrontEnd.sch, valve_indicatorV1.brd]
2021-04-07 AC changes
    Added 24V to 12V regulator for single 12V valve, routed, final error check. Update attributes and BOM.
    [TSAR_Actuator_Controller.brd, TSAR_Actuator_Controller.csv, TSAR_Actuator_Controller.sch]
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2021-04-07 POE, VI changes
    POE: corrected pad sizes for caps and inductor. Rerouted. Updated attributes and BOM. Final error check
    VI: changed name from valve_indicatorV1 to valve_indicator
    [POE_plus_input.brd, valve_indicator.brd, valve_indicator.csv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]
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2021-04-07 AC Error Check
    [TSAR_Actuator_Controller.brd]
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

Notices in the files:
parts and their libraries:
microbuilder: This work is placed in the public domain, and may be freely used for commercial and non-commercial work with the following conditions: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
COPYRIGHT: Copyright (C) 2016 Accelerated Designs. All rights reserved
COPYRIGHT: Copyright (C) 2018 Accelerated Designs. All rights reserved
